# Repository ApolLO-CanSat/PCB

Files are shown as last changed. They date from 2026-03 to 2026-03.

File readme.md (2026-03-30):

# Team ApolLO's CanSat PCBs
The mainboard features:
- **RP2350A** MCU 
- **W25Q128JVPIQ** flash memory
- **Waveshare 23721** for GPS signal
- **RFM98W 433MHz** LoRa module
- **MPU-6050** gyroscope and accelerometer
- **BMP 280** barometer and thermometer
- **USB-C connector**
- **BOOTSEL** and **RESET** buttons
- Status **LED**
- **Buzzer** for easier recovery
\
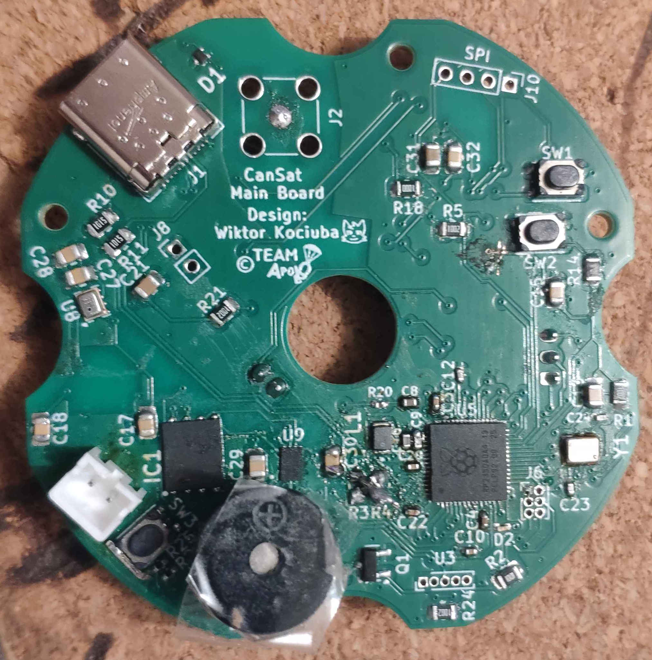
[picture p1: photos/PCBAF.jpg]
PCB Assembled Front

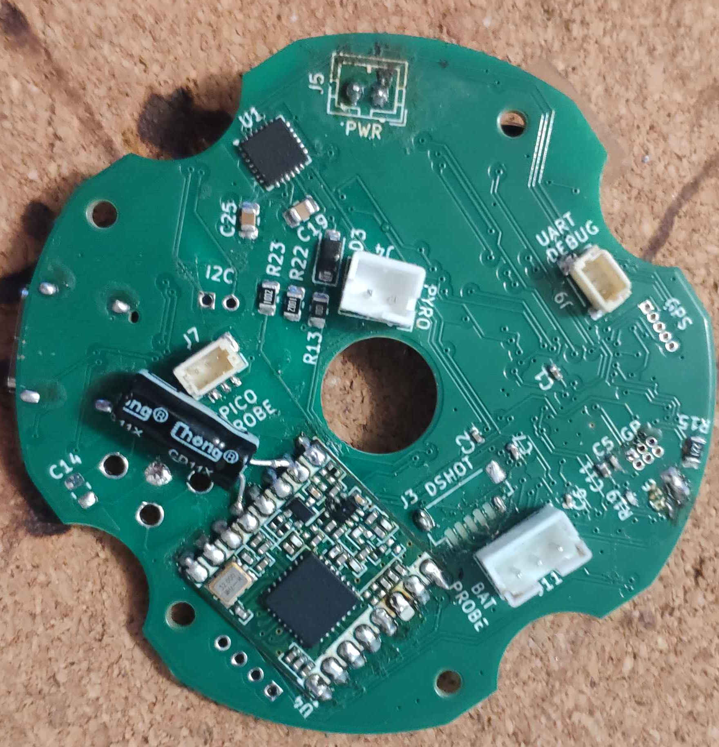
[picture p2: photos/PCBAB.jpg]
PCB Assembled Back

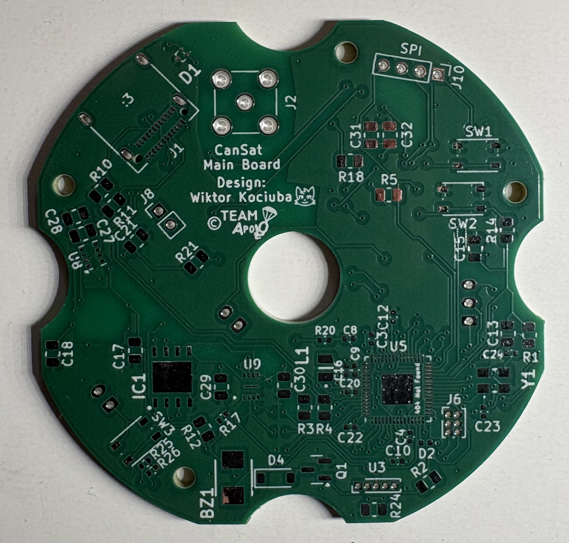
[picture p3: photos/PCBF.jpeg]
PCB Front

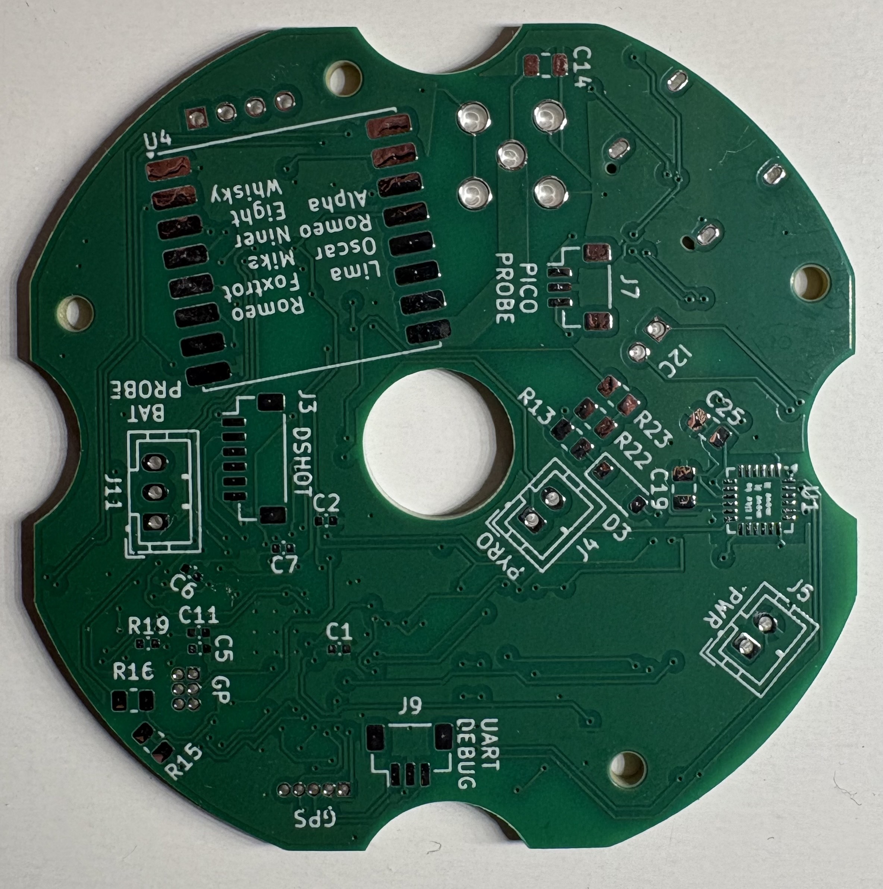
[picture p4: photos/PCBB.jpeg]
PCB Back

\
Mainboard schematic
MCU schematic
\
[Schematics in PDF file](https://github.com/ApolLO-CanSat/PCB/blob/main/schematics/CanSat.pdf)
\
PCB Schematic Front
PCB Schematic Back
\
[PCB schematic in PDF file](https://github.com/ApolLO-CanSat/PCB/blob/main/schematics/CanSatPCB.pdf)
---
## BOM
|Id|Designator|Footprint|Quantity|Designation|
|-|-|-|-|-|
|1|R5,R24,R12,R1,R21,R23,R22|R_0805_2012Metric|7|10K|
|2|R26,R25|R_0402_1005Metric|2|4.7K|
|3|C25|C_0805_2012Metric|1|10nF|
|4|R4,R3|R_0805_2012Metric|2|27|
|5|J8|PinHeader_1x02_P2.00mm_Vertical|1|Conn_01x02_Pin|
|6|L1|AOTAB201610S3R3101T|1|3.3u|
|7|D2|LED_0402_1005Metric|1|RED|
|8|U5|RP2350-QFN-60-1EP_7x7_P0.4mm_EP3.4x3.4mm_ThermalVias|1|RP2350_60QFN|
|9|C16,C9,C8,C11|C_0402_1005Metric|4|4.7uF|
|10|C20,C3,C4,C10,C22,C12,C7,C1,C5,C6,C2|C_0402_1005Metric|11|100nF|
|11|C24,C23|C_0402_1005Metric|2|15pF|
|12|C30,C15,C17,C32,C27,C28,C19|C_0805_2012Metric|7|100nF|
|13|BZ1|CMT-4023S|1|Buzzer|
|14|J1|USB_C_Receptacle_Amphenol_12401610E4-2A|1|USB_C_Receptacle|
|15|C31|C_0805_2012Metric|1|22u|
|16|SW2,SW1,SW3|SW_Push_1P1T_NO_Vertical_Wuerth_434133025816|3|SW_Push|
|17|IC1|SON127P600X500X80-9N-D|1|W25Q128JVPIQ|
|18|C21,C13|C_0805_2012Metric|2|1uF|
|19|D1|MMBT2907AM3T5G|1|ESD7L5.0DT5G|
|20|D4,D3|D_SOD-123|2|MBR0530T1G|
|21|R11,R10|R_0805_2012Metric|2|5.1K|
|22|J10|PinHeader_1x04_P2.00mm_Vertical|1|Conn_01x04_Pin|
|23|R18|R_0805_2012Metric|1|100|
|24|J2|SMA_Amphenol_901-144_Vertical|1|Conn_Coaxial|
|25|R17|R_0402_1005Metric|1|10K|
|26|R20|R_0402_1005Metric|1|33|
|27|U3|PinHeader_1x05_P1.00mm_Vertical|1|Waveshare23721|
|28|C18|C_0805_2012Metric|1|2.2nF|
|29|U8|Bosch_LGA-8_2x2.5mm_P0.65mm_ClockwisePinNumbering|1|BMP280|
|30|R2,R14,R13|R_0805_2012Metric|3|1K|
|31|Y1|ABM8272T3|1|ABM8272T3|
|32|C29|C_0805_2012Metric|1|2.2uF|
|33|Q1|SOT-23|1|BSS138|
|34|U9|PSON50P200X300X50-9N|1|APS6404L-3SQR-ZR|
|35|J6|PinHeader_2x03_P1.00mm_Vertical|1|Conn_01x06_Pin|
|36|R15|R_0805_2012Metric|1|220|
|37|J7|JST_SH_BM03B-SRSS-TB_1x03-1MP_P1.00mm_Vertical|1|Conn_01x03_Pin|
|38|R16|R_0805_2012Metric|1|DNC|
|39|J5|JST_PH_B2B-PH-K_1x02_P2.00mm_Vertical|1|Screw_Terminal_01x02|
|40|J9|JST_SH_BM03B-SRSS-TB_1x03-1MP_P1.00mm_Vertical|1|Conn_01x02_Pin|
|41|J11|JST_PH_B3B-PH-K_1x03_P2.00mm_Vertical|1|Conn_01x03_Socket|
|42|J3|JST_SH_BM06B-SRSS-TB_1x06-1MP_P1.00mm_Vertical|1|Conn_01x06_Socket|
|43|U4|HOPERF_RFM9XW_SMD|1|RFM98W-433S2|
|44|C14|C_0805_2012Metric|1|DNP|
|45|U1|InvenSense_QFN-24_4x4mm_P0.5mm|1|MPU-6050|
|46|J4|JST_PH_B2B-PH-K_1x02_P2.00mm_Vertical|1|Conn_01x02_Pin|
|47|R19|R_0402_1005Metric|1|1K|

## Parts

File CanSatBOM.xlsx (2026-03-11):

Id | Designator | Footprint | Quantity | Value | Manufacturer | Mfg Part # | Package | Type
1 | R4,R7,R3,R8,R9,R6,R5 | R_0805_2012Metric | 7 | 27 OHM | any available | any available | 0805(2012M) | SMD
2 | J8,J9,J4 | PinHeader_1x02_P1.00mm_Vertical | 3 | n/a | any available | any available | PinHeader_1x02_P1.00mm_Vertical | THT
3 | D2 | LED_0402_1005Metric | 1 | RED | any available | any available | 0402(1005M) | SMD
4 | U5 | RP2350-QFN-60-1EP_7x7_P0.4mm_EP3.4x3.4mm_ThermalVias | 1 | n/a | Raspberry Pi | RP2350A | SMD | SMD
5 | C30,C27,C28,C3,C4,C7,C10,C1,C5,C6,C12,C2 | CP_EIA-2012-15_AVX-P | 12 | 100nF | any available | any available | 2012-15M | SMD
6 | R23,R22,R12,R1,R2,R21 | R_0805_2012Metric | 6 | 10K OHM | any available | any available | 0805(2012M) | SMD
7 | BZ1 | MagneticBuzzer_Kingstate_KCG0601 | 1 | n/a | Kingstate | KCG0601 | THT | THT
8 | J1 | USB_C_Receptacle_Amphenol_12401610E4-2A | 1 | n/a | Amphenol | 12401610E4#2A | SMD | SMD
9 | C31 | CP_EIA-2012-15_AVX-P | 1 | 22uF | any available | any available | 2012-15M | SMD
10 | L1 | L_6.3x6.3_H3 | 1 | 3.3uH | any available | any available | L_6.3x6.3_H3 | SMD
11 | SW2,SW1,SW3 | SW_Push_1P1T_NO_Vertical_Wuerth_434133025816 | 3 | n/a | Wuerth | 434133025816 | SMD | SMD
12 | C15,C32 | CP_EIA-2012-15_AVX-P | 2 | 100nF | any available | any available | 2012-15M | SMD
13 | IC1 | SON127P600X500X80-9N-D | 1 | n/a | Winbond | W25Q128JVPIQ | SMD | SMD
14 | C21,C13,C14 | CP_EIA-2012-15_AVX-P | 3 | 1uF | any available | any available | 2012-15M | SMD
15 | C17 | CP_EIA-2012-15_AVX-P | 1 | 0.1uF | any available | any available | 2012-15M | SMD
16 | D1 | MMBT2907AM3T5G | 1 | n/a | onsemi | ESD7L5.0DT5G | SMD | SMD
17 | J7 | PinHeader_1x03_P1.00mm_Vertical | 1 | Conn_01x03_Pin | any available | any available | PinHeader_1x03_P1.00mm_Vertical | THT
18 | R11,R10 | R_0805_2012Metric | 2 | 5.1K Ohm | any available | any available | 0805(2012M) | SMD
19 | J10 | PinHeader_1x04_P1.00mm_Vertical | 1 | Conn_01x04_Pin | any available | any available | PinHeader_1x04_P1.00mm_Vertical | THT
20 | R18 | R_0805_2012Metric | 1 | 100 Ohm | any available | any available | 0805(2012M) | SMD
21 | C9,C16,C8,C11 | CP_EIA-2012-15_AVX-P | 4 | 4.7uF | any available | any available | 2012-15M | SMD
22 | J2 | SMA_Amphenol_901-144_Vertical | 1 | DNC | DNC | DNC | DNC | DNC
23 | R20 | R_0805_2012Metric | 1 | 33 Ohm | any available | any available | 0805(2012M) | SMD
24 | U3 | PinHeader_1x05_P1.00mm_Vertical | 1 | Conn_01x05_Pin | any available | any available | PinHeader_1x05_P1.00mm_Vertical | THT
25 | C18,C19 | CP_EIA-2012-15_AVX-P | 2 | 2.2nF | any available | any available | 2012-15M | SMD
26 | Y2 | ASE12000MHzET | 1 | n/a | Abracon | ASE-12.000MHz-E-T | SMD | SMD
27 | U8 | Bosch_LGA-8_2x2.5mm_P0.65mm_ClockwisePinNumbering | 1 | n/a | Bosch | BMP280 | SMD | SMD
28 | C29 | CP_EIA-2012-15_AVX-P | 1 | 2.2uF | any available | any available | 2012-15M | SMD
29 | U9 | PSON50P200X300X50-9N | 1 | n/a | AP Memory | APS6404L-3SQR-ZR | SMD | SMD
30 | J6 | PinHeader_2x03_P1.00mm_Vertical | 1 | Conn_01x06_Pin | any available | any available | PinHeader_2x03_P1.00mm_Vertical | THT
31 | R14,R13 | R_0805_2012Metric | 2 | 1K Ohm | any available | any available | 0805(2012M) | SMD
32 | R15 | R_0805_2012Metric | 1 | 220 Ohm | any available | any available | 0805(2012M) | SMD
33 | R16 | R_0805_2012Metric | 1 | DNC | DNC | DNC | DNC | DNC
34 | J5 | TerminalBlock_bornier-2_P5.08mm | 1 | Screw_Terminal_01x02 | any available | any available | Screw_Terminal_01x02 | THT
35 | J3 | JST_SH_BM06B-SRSS-TB_1x06-1MP_P1.00mm_Vertical | 1 | Conn_01x06_Socket | JST | BM06B-SRSS-TB (LF)(SN) | SMD | SMD
36 | U4 | HOPERF_RFM9XW_SMD | 1 | n/a | RF Solutions | RFM98W-433S2 | SMD | SMD
37 | D3 | D_SOD-123 | 1 | n/a | onsemi | MBR0530 | SMD | SMD
38 | U1 | InvenSense_QFN-24_4x4mm_P0.5mm | 1 | n/a | InvenSense | MPU-6050 | SMD | SMD

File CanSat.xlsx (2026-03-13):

Id | Designator | Footprint | Quantity | Designation | Part #
1 | R4,R7,R3,R8,R9,R6,R5 | R_0805_2012Metric | 7 | 27 | AC0805FR-0727RL | 0.039 | 0.273
2 | J8,J9,J4 | PinHeader_1x02_P1.00mm_Vertical | 3 | Conn_01x02_Pin |  |  | 0
3 | L1 | AOTAB201610S3R3101T | 1 | 3.3u | ISC1210ER3R3K | 2.4 | 2.4
4 | D2 | LED_0402_1005Metric | 1 | RED | IN-S42DS5G | 1.55 | 1.55
5 | U5 | RP2350-QFN-60-1EP_7x7_P0.4mm_EP3.4x3.4mm_ThermalVias | 1 | RP2350_60QFN | SC1509(13)-A4 | 2.97 | 2.97
6 | C16,C9,C8,C11 | C_0402_1005Metric | 4 | 4.7uF | 0402ZD475KAT2A | 0.593 | 2.372
7 | C20,C3,C4,C10,C22,C12,C7,C1,C5,C6,C2 | C_0402_1005Metric | 11 | 100nF | 0402ZC104KAT4A | 0.12 | 1.32
8 | C24,C23 | C_0402_1005Metric | 2 | 15pF | C0402C150F8HACTU | 0.628 | 1.256
9 | C30,C15,C17,C32,C27,C28 | CP_EIA-2012-15_AVX-P | 6 | 100nF | KAF21BR71H104JM | 0.335 | 2.01
10 | BZ1 | CMT-4023S | 1 | Buzzer | CMT-4023S-SMT-TR | 11.35 | 11.35
11 | J1 | USB_C_Receptacle_Amphenol_12401610E4-2A | 1 | USB_C_Receptacle | 12401610E4#2A | 5.33 | 5.33
12 | C31 | CP_EIA-2012-15_AVX-P | 1 | 22u | CL21A226MQQNNNE | 0.482 | 0.482
13 | SW2,SW1,SW3 | SW_Push_1P1T_NO_Vertical_Wuerth_434133025816 | 3 | SW_Push | 434133025816 | 2.03 | 6.09
14 | IC1 | SON127P600X500X80-9N-D | 1 | W25Q128JVPIQ | W25Q128JVPIQ | 8.51 | 8.51
15 | C21,C13 | CP_EIA-2012-15_AVX-P | 2 | 1uF | 0805YC105KAT2A | 0.37 | 0.74
16 | R12,R1,R21,R23,R22 | R_0805_2012Metric | 5 | 10K | AC0805DR-0710KL | 0.112 | 0.56
17 | D1 | MMBT2907AM3T5G | 1 | ESD7L5.0DT5G | ESD7L5.0DT5G | 4.21 | 4.21
18 | J7 | PinHeader_1x03_P1.00mm_Vertical | 1 | Conn_01x03_Pin |  |  | 0
19 | R11,R10 | R_0805_2012Metric | 2 | 5.1K | RC0805FR-075K1L | 0.37 | 0.74
20 | J10 | PinHeader_1x04_P1.00mm_Vertical | 1 | Conn_01x04_Pin |  |  | 0
21 | R18 | R_0805_2012Metric | 1 | 100 | RC0805FR-07100RL | 0.37 | 0.37
22 | J2 | SMA_Amphenol_901-144_Vertical | 1 | Conn_Coaxial |  |  | 0
23 | R17 | R_0402_1005Metric | 1 | 10K | RCA040210K0JNED | 0.142 | 0.142
24 | R20 | R_0402_1005Metric | 1 | 33 | SFR01MZPJ330 | 0.555 | 0.555
25 | U3 | PinHeader_1x05_P1.00mm_Vertical | 1 | Waveshare23721 |  |  | 0
26 | C18,C19 | CP_EIA-2012-15_AVX-P | 2 | 2.2nF | 08055C222M4T2A | 0.778 | 1.556
27 | U8 | Bosch_LGA-8_2x2.5mm_P0.65mm_ClockwisePinNumbering | 1 | BMP280 | BMP280 |  | 0
28 | Y1 | ABM8272T3 | 1 | ABM8272T3 | ABM8-272-T3 | 2 | 2
29 | C29 | CP_EIA-2012-15_AVX-P | 1 | 2.2uF | 0805X225M100CT | 0.512 | 0.512
30 | U9 | PSON50P200X300X50-9N | 1 | APS6404L-3SQR-ZR | APS6404L-3SQR-ZR | 8.08 | 8.08
31 | J6 | PinHeader_2x03_P1.00mm_Vertical | 1 | Conn_01x06_Pin |  |  | 0
32 | R14,R13 | R_0805_2012Metric | 2 | 1K | 1623131-1 | 0.37 | 0.74
33 | R15 | R_0805_2012Metric | 1 | 220 | RC0805JR-13220RL | 0.026 | 0.026
34 | R16 | R_0805_2012Metric | 1 | DNC |  |  | 0
35 | J5 | TerminalBlock_bornier-2_P5.08mm | 1 | Screw_Terminal_01x02 |  |  | 0
36 | J3 | JST_SH_BM06B-SRSS-TB_1x06-1MP_P1.00mm_Vertical | 1 | Conn_01x06_Socket | BM06B-SRSS-TB(LF)(SN) | 3.33 | 3.33
37 | U4 | HOPERF_RFM9XW_SMD | 1 | RFM98W-433S2 | RFM98W-433S2 |  | 0
38 | D3 | D_SOD-123 | 1 | MBR0530 | MBR0530T1G | 0.516 | 0.516
39 | U1 | InvenSense_QFN-24_4x4mm_P0.5mm | 1 | MPU-6050 | MPU-6050 |  | 0
40 | R19 | R_0402_1005Metric | 1 | 1K | MCS04020C1001FE000 | 0.086 | 0.086
 |  |  |  |  |  |  | 70.076
 |  |  |  |  |  | Quantity | 2
 |  |  |  |  |  |  | 140.152

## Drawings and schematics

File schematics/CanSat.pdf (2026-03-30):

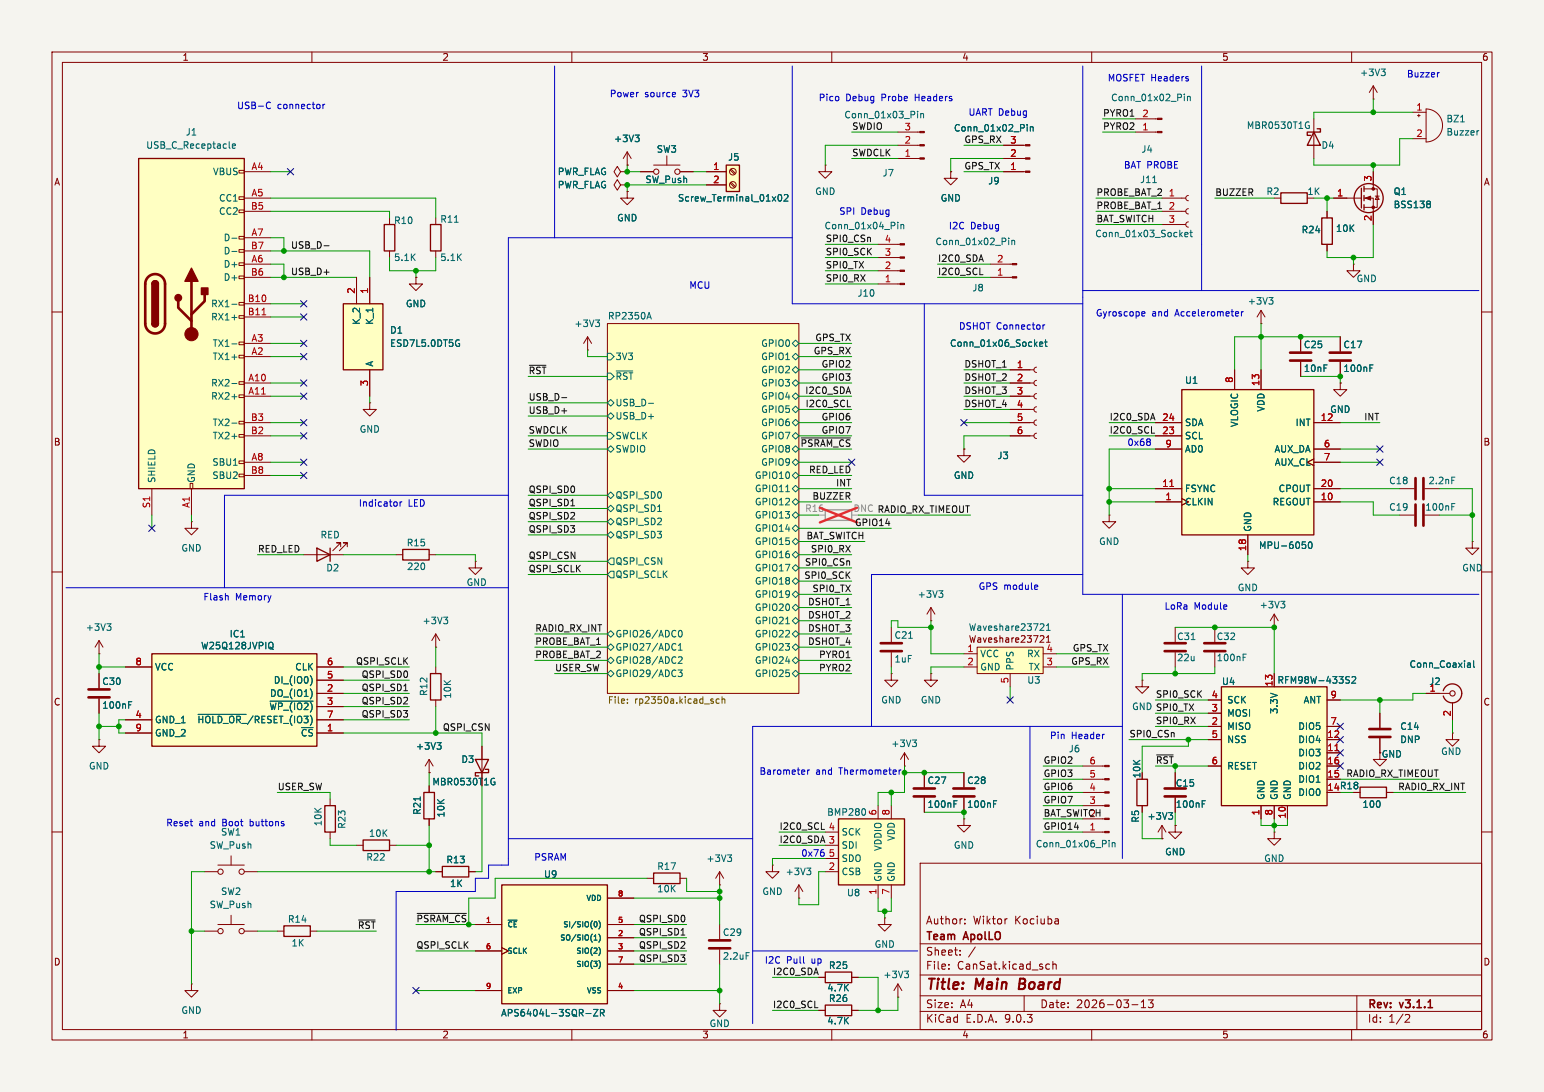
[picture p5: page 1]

Reset and Boot buttons

File: CanSat.kicad_sch Sheet: / Team ApolLO

Id: 1/2 Title: Main Board

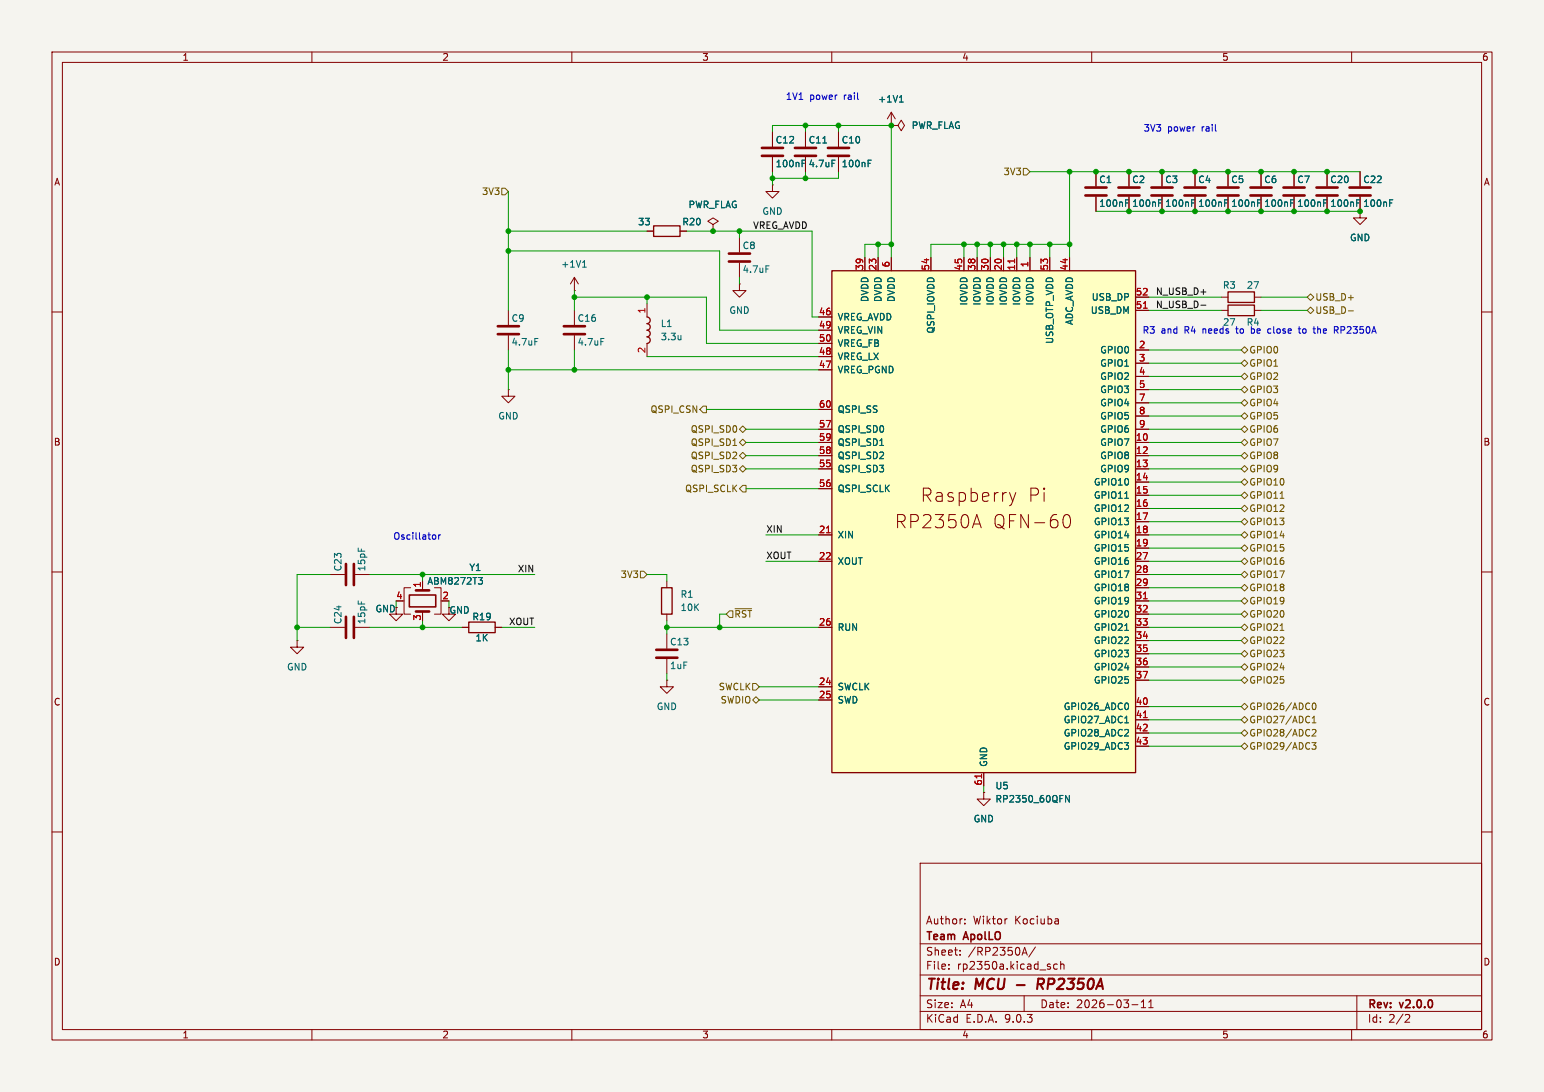
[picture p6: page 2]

6 QSPI_IOVDD 54 IOVDD 45 IOVDD 38 GND 61 IOVDD 30 IOVDD 20 IOVDD 11 IOVDD

File: rp2350a.kicad_sch Sheet: /RP2350A/ Team ApolLO

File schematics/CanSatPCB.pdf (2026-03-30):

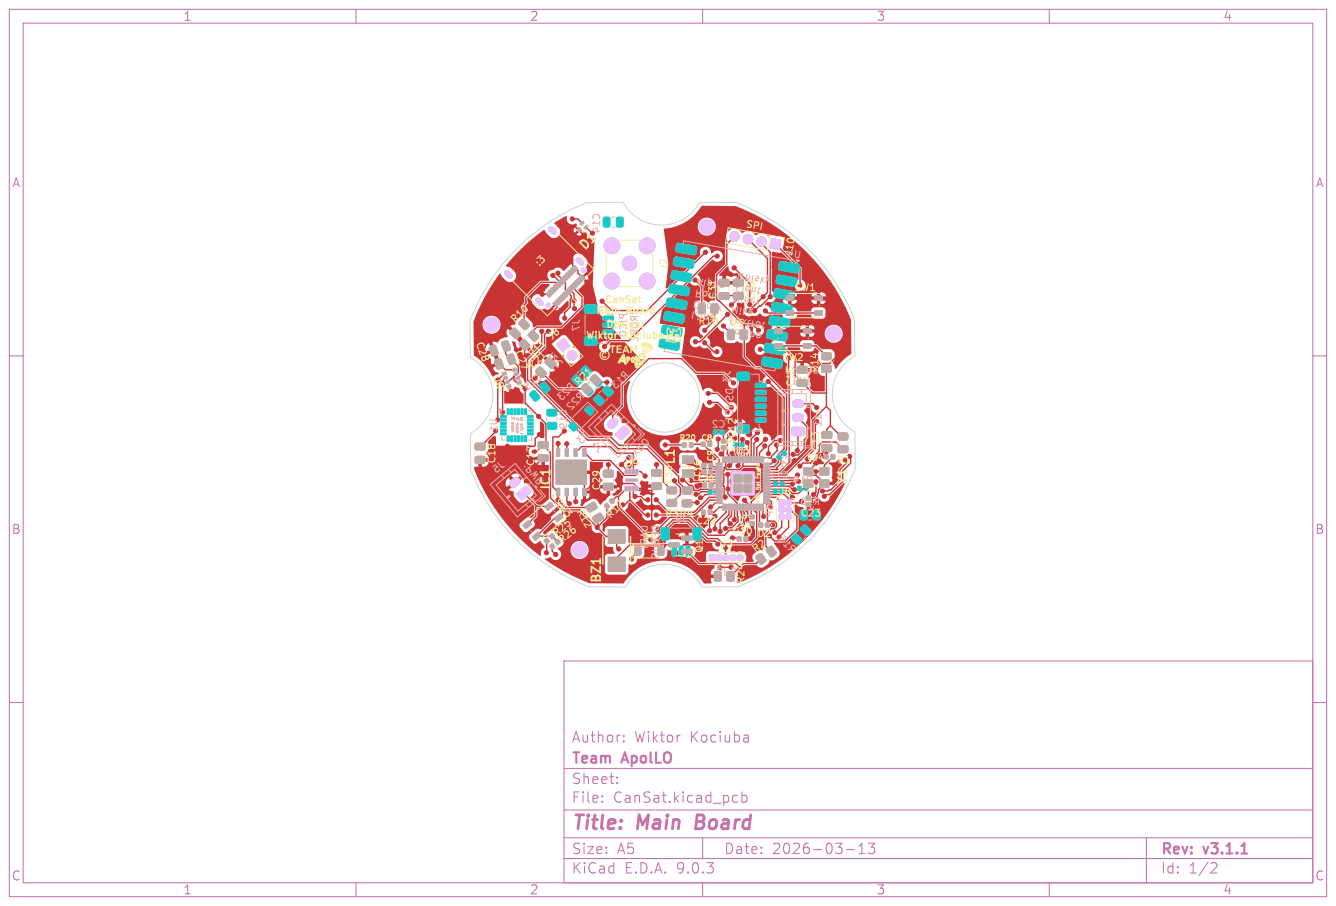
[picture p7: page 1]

File: CanSat.kicad_pcb Sheet: Team ApolLO

Id: 1/2 Title: Main Board

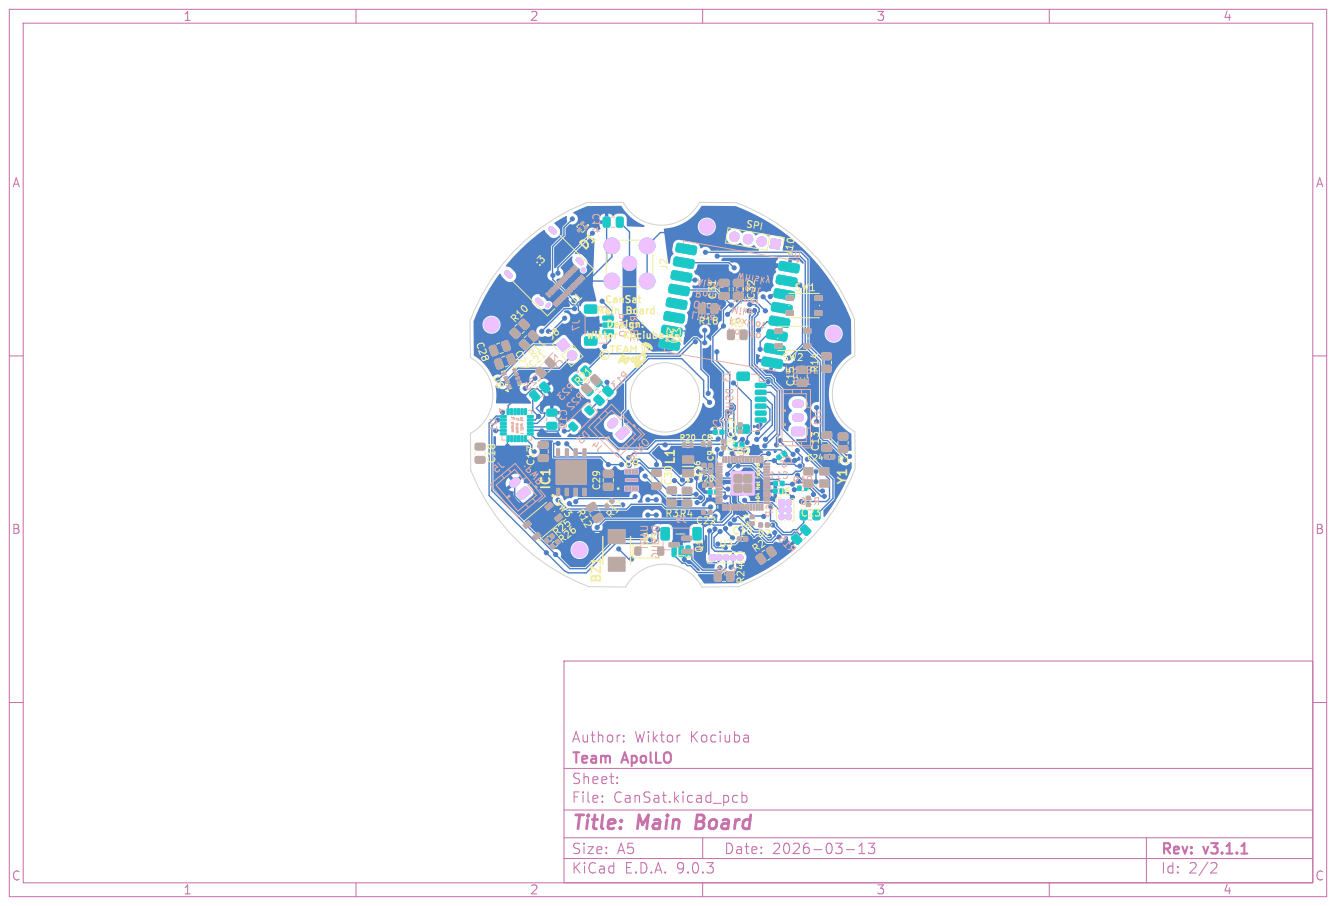
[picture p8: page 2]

File: CanSat.kicad_pcb Sheet: Team ApolLO

Id: 2/2 Title: Main Board

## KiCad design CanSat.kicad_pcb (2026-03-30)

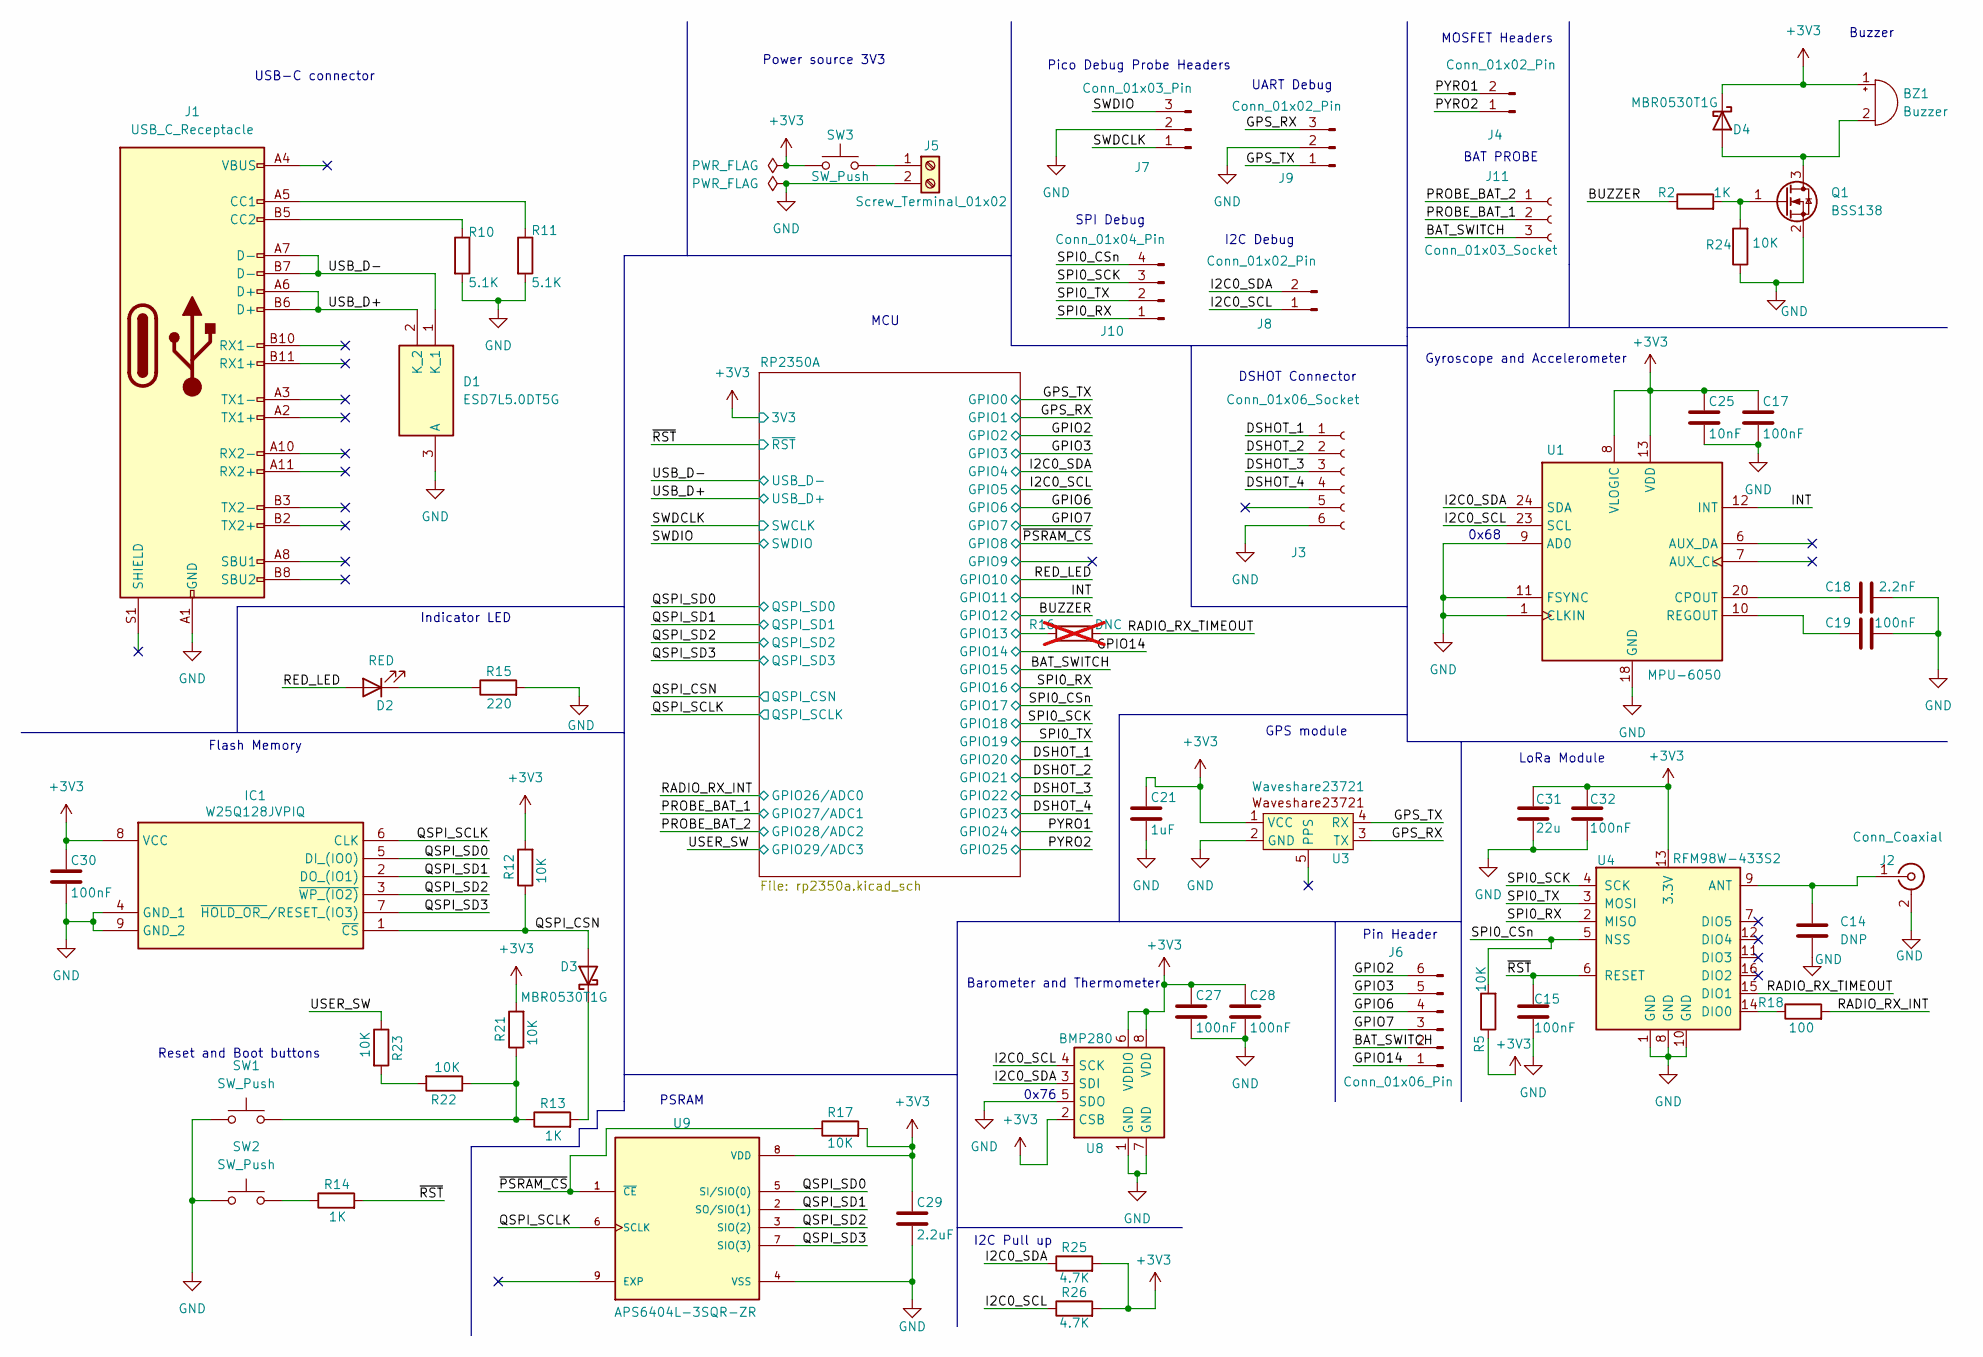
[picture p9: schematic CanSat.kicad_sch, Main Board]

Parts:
BZ1: Buzzer; CMT-4023S
C14: DNP; C_0805_2012Metric
C15, C17, C19, C27, C28, C30, C32: 100nF; C_0805_2012Metric
C18: 2.2nF; C_0805_2012Metric
C21: 1uF; C_0805_2012Metric
C25: 10nF; C_0805_2012Metric
C29: 2.2uF; C_0805_2012Metric
C31: 22u; C_0805_2012Metric
D1: ESD7L5.0DT5G; MMBT2907AM3T5G; Mouser Part Number 863-ESD7L5.0DT5G
D2: RED; LED_0402_1005Metric
D3, D4: MBR0530T1G; D_SOD-123
IC1: W25Q128JVPIQ; SON127P600X500X80-9N-D; Mouser Part Number 454-W25Q128JVPIQ
J1: USB_C_Receptacle; USB_C_Receptacle_Amphenol_12401610E4-2A
J2: Conn_Coaxial; SMA_Amphenol_901-144_Vertical
J3: Conn_01x06_Socket; JST_SH_BM06B-SRSS-TB_1x06-1MP_P1.00mm_Vertical
J4: Conn_01x02_Pin; JST_PH_B2B-PH-K_1x02_P2.00mm_Vertical
J5: Screw_Terminal_01x02; JST_PH_B2B-PH-K_1x02_P2.00mm_Vertical
J6: Conn_01x06_Pin; PinHeader_2x03_P1.00mm_Vertical
J7: Conn_01x03_Pin; JST_SH_BM03B-SRSS-TB_1x03-1MP_P1.00mm_Vertical
J8: Conn_01x02_Pin; PinHeader_1x02_P2.00mm_Vertical
J9: Conn_01x02_Pin; JST_SH_BM03B-SRSS-TB_1x03-1MP_P1.00mm_Vertical
J10: Conn_01x04_Pin; PinHeader_1x04_P2.00mm_Vertical
J11: Conn_01x03_Socket; JST_PH_B3B-PH-K_1x03_P2.00mm_Vertical
Q1: BSS138; SOT-23
R2, R13, R14: 1K; R_0805_2012Metric
R5, R12, R21, R22, R23, R24: 10K; R_0805_2012Metric
R10, R11: 5.1K; R_0805_2012Metric
R15: 220; R_0805_2012Metric
R16: DNC; R_0805_2012Metric; not fitted
R17: 10K; R_0402_1005Metric
R18: 100; R_0805_2012Metric
R25, R26: 4.7K; R_0402_1005Metric
SW1, SW2, SW3: SW_Push; SW_Push_1P1T_NO_Vertical_Wuerth_434133025816
U1: MPU-6050; InvenSense_QFN-24_4x4mm_P0.5mm
U3: Waveshare23721; PinHeader_1x05_P1.00mm_Vertical
U4: RFM98W-433S2; HOPERF_RFM9XW_SMD
U8: BMP280; Bosch_LGA-8_2x2.5mm_P0.65mm_ClockwisePinNumbering
U9: APS6404L-3SQR-ZR; PSON50P200X300X50-9N; PARTREV 2.3

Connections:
+3V3: BZ1.1 (+), C17.1, C21.1, C25.1, C27.1, C28.1, C29.1, C30.1, C31.1, C32.1, D4.1 (K), IC1.8 (VCC), R5.1, R12.2, R17.2, R21.2, R25.2, R26.2, SW3.1, U1.8 (VLOGIC), U1.13 (VDD), U3.1 (VCC), U4.13 (3.3V), U8.2 (CSB), U8.6 (VDDIO), U8.8 (VDD), U9.8 (VDD); also elsewhere on the board
/BAT_SWITCH: J6.2, J11.3; also elsewhere on the board
/BUZZER: R2.1; also elsewhere on the board
/DSHOT_1: J3.1; also elsewhere on the board
/DSHOT_2: J3.2; also elsewhere on the board
/DSHOT_3: J3.3; also elsewhere on the board
/DSHOT_4: J3.4; also elsewhere on the board
/GPIO2: J6.6; also elsewhere on the board
/GPIO3: J6.5; also elsewhere on the board
/GPIO6: J6.4; also elsewhere on the board
/GPIO7: J6.3; also elsewhere on the board
/GPIO14: J6.1; also elsewhere on the board
/GPS_RX: J9.3, U3.3 (TX); also elsewhere on the board
/GPS_TX: J9.1, U3.4 (RX); also elsewhere on the board
/I2C0_SCL: J8.1, R26.1, U1.23 (SCL), U8.4 (SCK); also elsewhere on the board
/I2C0_SDA: J8.2, R25.1, U1.24 (SDA), U8.3 (SDI); also elsewhere on the board
/INT: U1.12 (INT); also elsewhere on the board
/PROBE_BAT_1: J11.2; also elsewhere on the board
/PROBE_BAT_2: J11.1; also elsewhere on the board
/PYRO1: J4.2; also elsewhere on the board
/PYRO2: J4.1; also elsewhere on the board
/QSPI_CSN: D3.2 (A), IC1.1 (~CS), R12.1; also elsewhere on the board
/QSPI_SCLK: IC1.6 (CLK), U9.6 (SCLK); also elsewhere on the board
/QSPI_SD0: IC1.5 (DI_(IO0)), U9.5 (SI/SIO(0)); also elsewhere on the board
/QSPI_SD1: IC1.2 (DO_(IO1)), U9.2 (SO/SIO(1)); also elsewhere on the board
/QSPI_SD2: IC1.3 (~WP_(IO2)), U9.3 (SIO(2)); also elsewhere on the board
/QSPI_SD3: IC1.7 (~HOLD_OR_/RESET_(IO3)), U9.7 (SIO(3)); also elsewhere on the board
/RADIO_RX_INT: R18.2; also elsewhere on the board
/RADIO_RX_TIMEOUT: R16.2, U4.15 (DIO1)
/RED_LED: D2.2 (A); also elsewhere on the board
/RP2350A/GPIO13: R16.1; also elsewhere on the board
/SPI0_CSn: J10.4, R5.2, U4.5 (NSS); also elsewhere on the board
/SPI0_RX: J10.1, U4.2 (MISO); also elsewhere on the board
/SPI0_SCK: J10.3, U4.4 (SCK); also elsewhere on the board
/SPI0_TX: J10.2, U4.3 (MOSI); also elsewhere on the board
/SWDCLK: J7.1; also elsewhere on the board
/SWDIO: J7.3; also elsewhere on the board
/USB_D+: D1.2 (K_2), J1.A6 (D+), J1.B6 (D+); also elsewhere on the board
/USB_D-: D1.1 (K_1), J1.A7 (D-), J1.B7 (D-); also elsewhere on the board
/USER_SW: R23.1; also elsewhere on the board
/~PSRAM_CS: R17.1, U9.1 (~CE); also elsewhere on the board
/~RST: C15.1, R14.2, U4.6 (RESET); also elsewhere on the board
GND: C14.1, C15.2, C17.2, C18.2, C19.2, C21.2, C25.2, C27.2, C28.2, C29.2, C30.2, C31.2, C32.2, D1.3 (A), IC1.4 (GND_1), IC1.9 (GND_2), J1.A1 (GND), J1.A12 (GND), J1.B1 (GND), J1.B12 (GND), J2.2 (Ext), J3.6, J5.2, J7.2, J9.2, Q1.2 (S), R10.2, R11.2, R15.2, R24.1, SW1.1, SW2.1, U1.1 (CLKIN), U1.9 (AD0), U1.11 (FSYNC), U1.18 (GND), U3.2 (GND), U4.1 (GND), U4.8 (GND), U4.10 (GND), U8.1 (GND), U8.5 (SDO), U8.7 (GND), U9.4 (VSS); also elsewhere on the board
unnamed: BZ1.2 (-), D4.2 (A), Q1.3 (D)
unnamed: D2.1 (K), R15.1
unnamed: D3.1 (K), R13.2
unnamed: J1.A5 (CC1), R11.1
unnamed: J1.B5 (CC2), R10.1
unnamed: C14.2, J2.1 (In), U4.9 (ANT)
unnamed: J5.1, SW3.2
unnamed: Q1.1 (G), R2.2, R24.2
unnamed: R13.1, R21.1, R22.1, SW1.2
unnamed: R14.1, SW2.2
unnamed: R22.2, R23.2
unnamed: C18.1, U1.20 (CPOUT)
unnamed: C19.1, U1.10 (REGOUT)
unnamed: R18.1, U4.14 (DIO0)

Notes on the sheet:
I2C Pull up
0x68
BAT PROBE
UART Debug
Buzzer
Gyroscope and Accelerometer
Reset and Boot buttons
GPS module
LoRa Module
MOSFET Headers
Power source 3V3
Pin Header
I2C Debug
PSRAM
Pico Debug Probe Headers
MCU
0x76
SPI Debug
Barometer and Thermometer
USB-C connector
Indicator LED
Flash Memory
DSHOT Connector

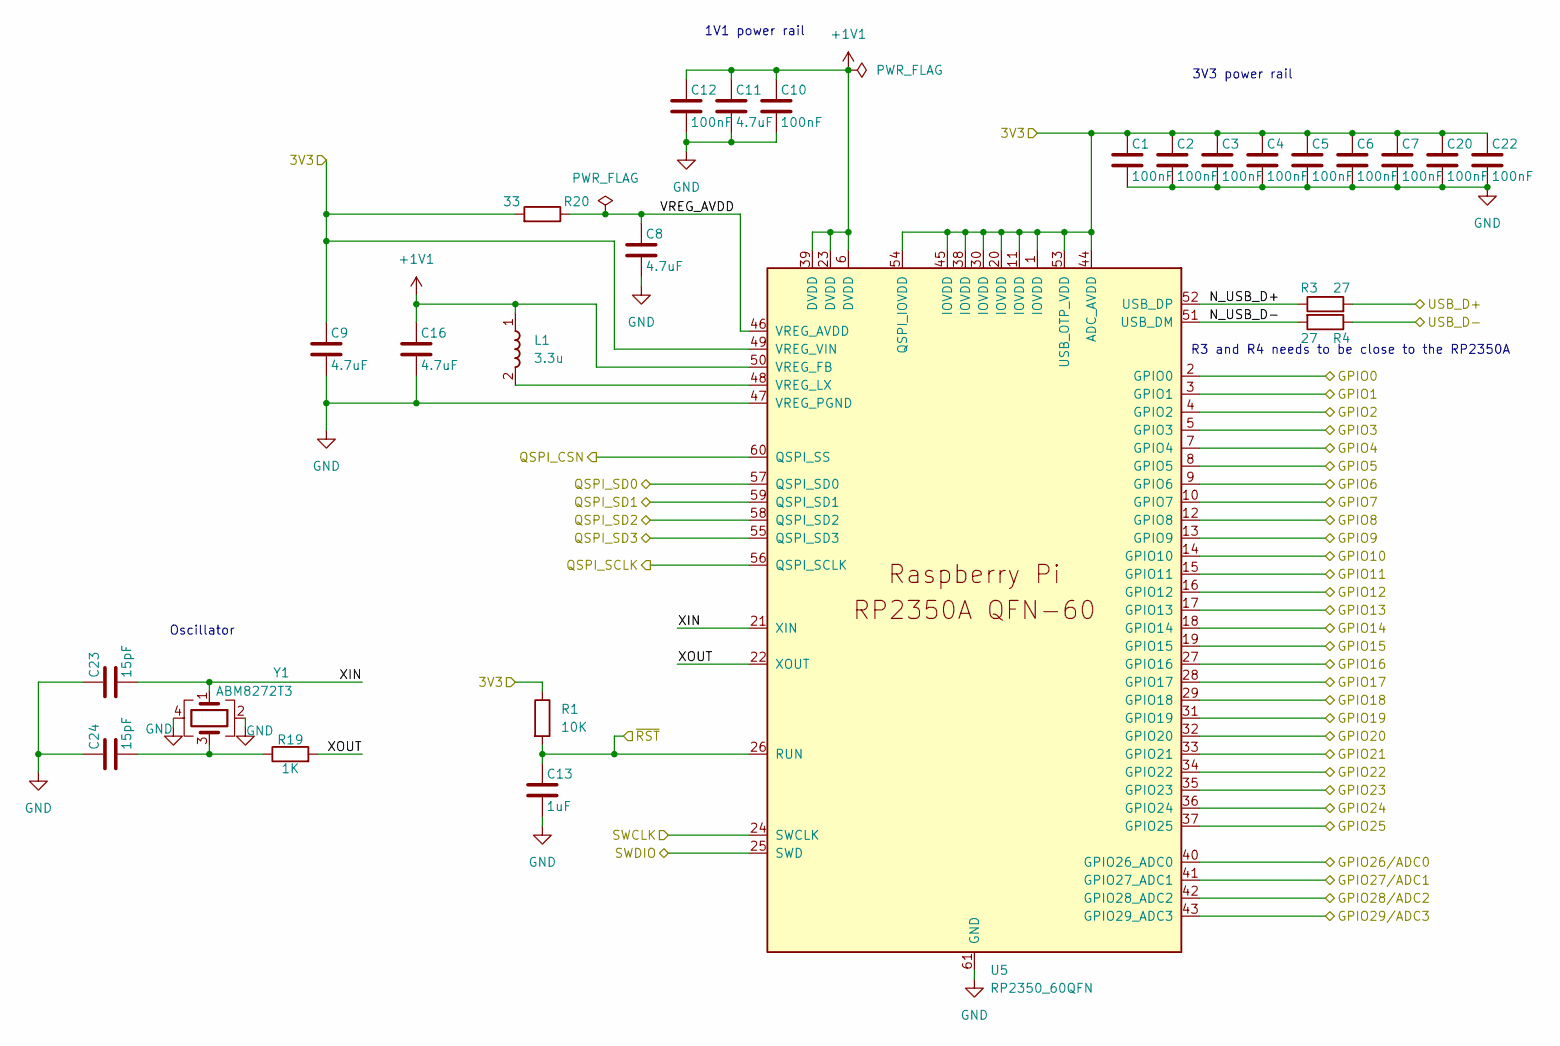
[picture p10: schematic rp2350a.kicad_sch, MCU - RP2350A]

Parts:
C1, C2, C3, C4, C5, C6, C7, C10, C12, C20, C22: 100nF; C_0402_1005Metric
C8, C9, C11, C16: 4.7uF; C_0402_1005Metric
C13: 1uF; C_0805_2012Metric
C23, C24: 15pF; C_0402_1005Metric
L1: 3.3u; AOTAB201610S3R3101T; Mouser Part Number 815-AB201610S3R3101T
R1: 10K; R_0805_2012Metric
R3, R4: 27; R_0805_2012Metric
R19: 1K; R_0402_1005Metric
R20: 33; R_0402_1005Metric
U5: RP2350_60QFN; RP2350-QFN-60-1EP_7x7_P0.4mm_EP3.4x3.4mm_ThermalVias
Y1: ABM8272T3

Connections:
+1V1: C10.1, C11.1, C12.1, C16.1, L1.1, U5.6 (DVDD), U5.23 (DVDD), U5.39 (DVDD), U5.50 (VREG_FB)
+3V3: C1.1, C2.1, C3.1, C4.1, C5.1, C6.1, C7.1, C9.1, C20.1, C22.1, R1.1, R20.2, U5.1 (IOVDD), U5.11 (IOVDD), U5.20 (IOVDD), U5.30 (IOVDD), U5.38 (IOVDD), U5.44 (ADC_AVDD), U5.45 (IOVDD), U5.49 (VREG_VIN), U5.53 (USB_OTP_VDD), U5.54 (QSPI_IOVDD); also elsewhere on the board
/BAT_SWITCH: U5.19 (GPIO15); also elsewhere on the board
/BUZZER: U5.16 (GPIO12); also elsewhere on the board
/DSHOT_1: U5.32 (GPIO20); also elsewhere on the board
/DSHOT_2: U5.33 (GPIO21); also elsewhere on the board
/DSHOT_3: U5.34 (GPIO22); also elsewhere on the board
/DSHOT_4: U5.35 (GPIO23); also elsewhere on the board
/GPIO2: U5.4 (GPIO2); also elsewhere on the board
/GPIO3: U5.5 (GPIO3); also elsewhere on the board
/GPIO6: U5.9 (GPIO6); also elsewhere on the board
/GPIO7: U5.10 (GPIO7); also elsewhere on the board
/GPIO14: U5.18 (GPIO14); also elsewhere on the board
/GPS_RX: U5.3 (GPIO1); also elsewhere on the board
/GPS_TX: U5.2 (GPIO0); also elsewhere on the board
/I2C0_SCL: U5.8 (GPIO5); also elsewhere on the board
/I2C0_SDA: U5.7 (GPIO4); also elsewhere on the board
/INT: U5.15 (GPIO11); also elsewhere on the board
/PROBE_BAT_1: U5.41 (GPIO27_ADC1); also elsewhere on the board
/PROBE_BAT_2: U5.42 (GPIO28_ADC2); also elsewhere on the board
/PYRO1: U5.36 (GPIO24); also elsewhere on the board
/PYRO2: U5.37 (GPIO25); also elsewhere on the board
/QSPI_CSN: U5.60 (QSPI_SS); also elsewhere on the board
/QSPI_SCLK: U5.56 (QSPI_SCLK); also elsewhere on the board
/QSPI_SD0: U5.57 (QSPI_SD0); also elsewhere on the board
/QSPI_SD1: U5.59 (QSPI_SD1); also elsewhere on the board
/QSPI_SD2: U5.58 (QSPI_SD2); also elsewhere on the board
/QSPI_SD3: U5.55 (QSPI_SD3); also elsewhere on the board
/RADIO_RX_INT: U5.40 (GPIO26_ADC0); also elsewhere on the board
/RED_LED: U5.14 (GPIO10); also elsewhere on the board
/RP2350A/GPIO9: U5.13 (GPIO9)
/RP2350A/GPIO13: U5.17 (GPIO13); also elsewhere on the board
/RP2350A/N_USB_D+: R3.1, U5.52 (USB_DP)
/RP2350A/N_USB_D-: R4.2, U5.51 (USB_DM)
/RP2350A/VREG_AVDD: C8.1, R20.1, U5.46 (VREG_AVDD)
/RP2350A/XIN: C23.2, U5.21 (XIN), Y1.1
/RP2350A/XOUT: R19.2, U5.22 (XOUT)
/SPI0_CSn: U5.28 (GPIO17); also elsewhere on the board
/SPI0_RX: U5.27 (GPIO16); also elsewhere on the board
/SPI0_SCK: U5.29 (GPIO18); also elsewhere on the board
/SPI0_TX: U5.31 (GPIO19); also elsewhere on the board
/SWDCLK: U5.24 (SWCLK); also elsewhere on the board
/SWDIO: U5.25 (SWD); also elsewhere on the board
/USB_D+: R3.2; also elsewhere on the board
/USB_D-: R4.1; also elsewhere on the board
/USER_SW: U5.43 (GPIO29_ADC3); also elsewhere on the board
/~PSRAM_CS: U5.12 (GPIO8); also elsewhere on the board
/~RST: C13.1, R1.2, U5.26 (RUN); also elsewhere on the board
GND: C1.2, C2.2, C3.2, C4.2, C5.2, C6.2, C7.2, C8.2, C9.2, C10.2, C11.2, C12.2, C13.2, C16.2, C20.2, C22.2, C23.1, C24.1, U5.47 (VREG_PGND), U5.61 (GND), Y1.2, Y1.4; also elsewhere on the board
unnamed: C24.2, R19.1, Y1.3
unnamed: L1.2, U5.48 (VREG_LX)

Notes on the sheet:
1V1 power rail
R3 and R4 needs to be close to the RP2350A
3V3 power rail
Oscillator

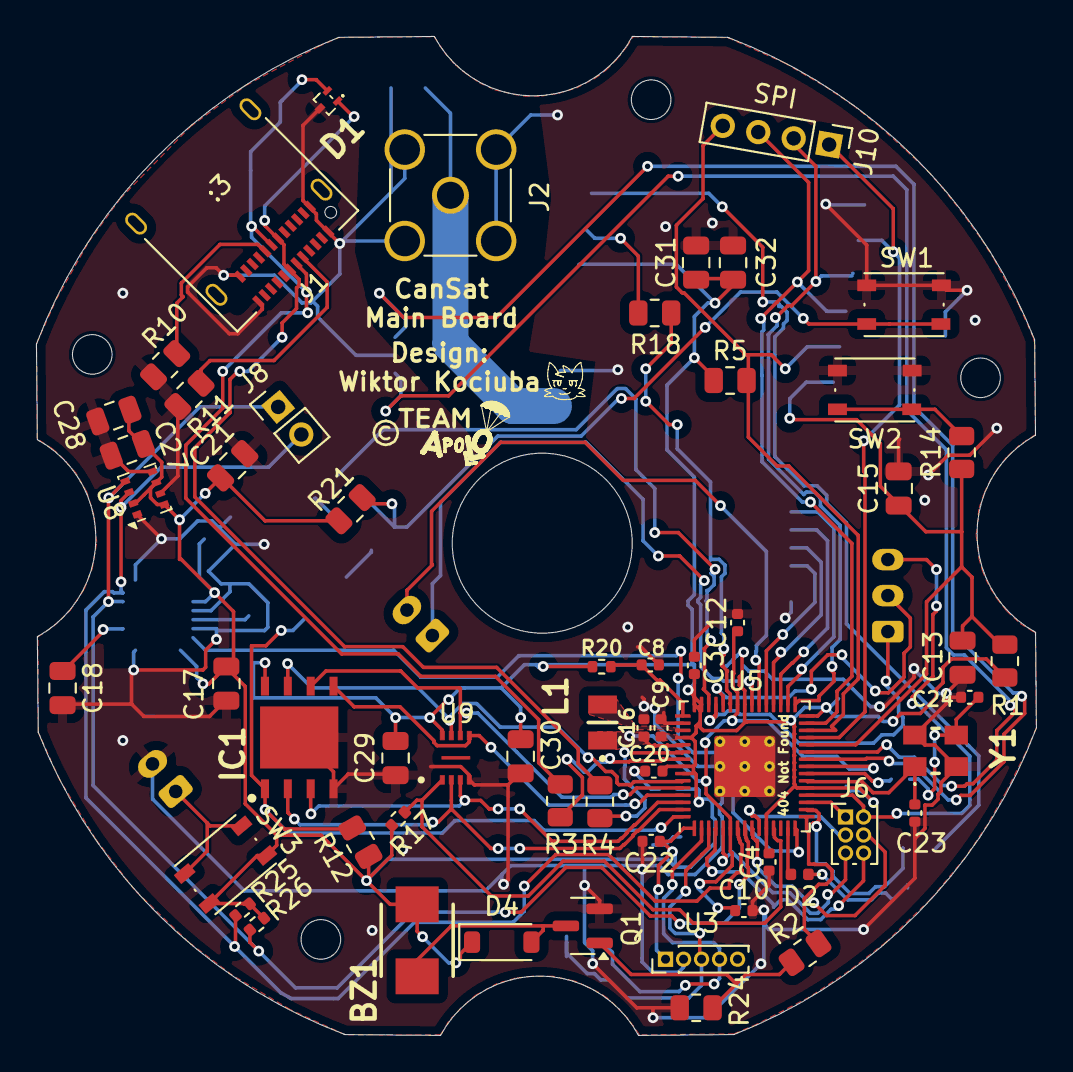
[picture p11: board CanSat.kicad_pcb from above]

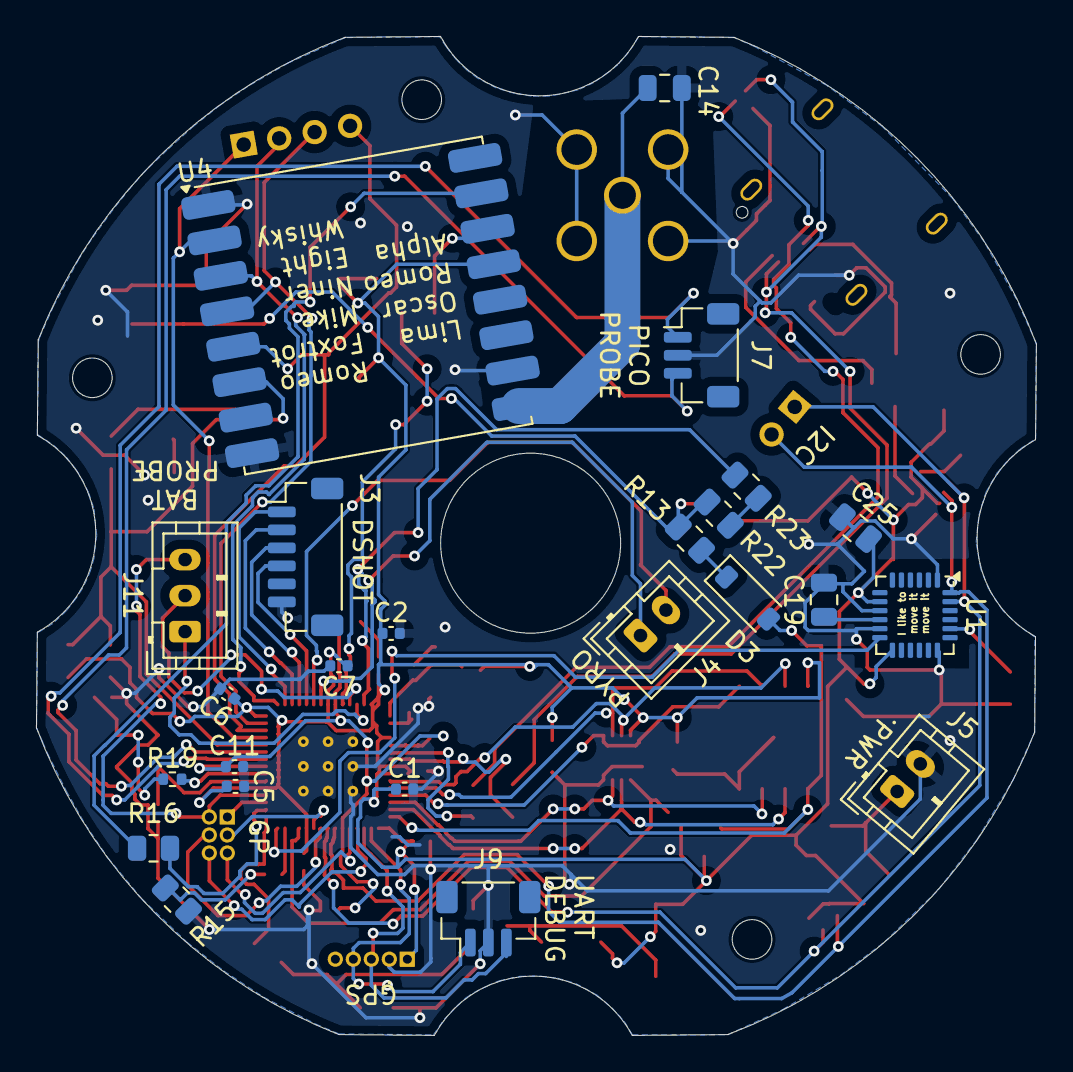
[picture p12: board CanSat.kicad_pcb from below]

Board: 2 copper layers, 55.6 x 55.5 mm, 84 parts (24 on the bottom side), 65 nets.

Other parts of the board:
M2, M2#2: MountingHole_2.2mm_M2

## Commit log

2025-11-21 Add new flash memory and PSRAM
    [CanSat.kicad_sch, radio.kicad_sch]
2025-11-21 Add new LoRa module
    [CanSat.kicad_sch, radio.kicad_sch]
2025-11-21 Assigned footprints and drew pcb outline
    [CanSat.kicad_pcb, CanSat.kicad_sch, radio.kicad_sch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]
2025-11-22 Add components to pcb
    Added:
    3V3 power source
    USB-C connector
    Flash memory and PSRAM
    [CanSat.kicad_pcb, CanSat.kicad_sch]
2025-12-10 Connected LoRa
    [CanSat.kicad_pcb, CanSat.kicad_sch]
2025-12-10 Added more components to the pcb
    [CanSat.kicad_pcb]
2025-12-10 Connected all components
    [CanSat.kicad_pcb]
2025-12-10 Rotated LoRa and updated readme
    [CanSat.kicad_pcb]
2025-12-15 Update of pcb
    [CanSat.kicad_pcb]
2026-01-22 Changed LoRa module to RFM98W 433MHz
    [CanSat.kicad_pcb, CanSat.kicad_sch, radio.kicad_sch]
2026-01-22 Fixed silkscreen overlap
    [CanSat.kicad_pcb]
2026-01-26 Added pin headers, debug headers, changed power source
    [CanSat.kicad_pcb, CanSat.kicad_sch]
2026-02-17 Added BOM to readme
    [CanSat.kicad_sch]
2026-03-07 Changed LoRa footprint + signed the PCB + added a on/off button
    [CanSat.kicad_pcb, CanSat.kicad_sch]
2026-03-11 Fixed design flaw with with components that MCU depends on
    [CanSat-CuBottom.gbr, CanSat-CuTop.gbr, CanSat-EdgeCuts.gbr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]
2026-03-13 Changed connectors
    [CanSat-CuBottom.gbr, CanSat-CuTop.gbr, CanSat-EdgeCuts.gbr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]
2026-03-13 Readme Update
    [CanSat-CuBottom.gbr, CanSat-CuTop.gbr, CanSat-EdgeCuts.gbr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]
2026-03-13 changed buzzer circuit and capacitor footprints
    [CanSat.kicad_pcb, CanSat.kicad_sch, rp2350a.kicad_sch]
2026-03-13 added Q1 part number
    [CanSat.kicad_pcb, CanSat.kicad_sch]
2026-03-13 updated spacing
    [CanSat-CuBottom.gbr, CanSat-CuTop.gbr, CanSat-EdgeCuts.gbr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]
2026-03-13 Changed QSPI and added pull-ups on i2c
    [CanSat-CuBottom.gbr, CanSat-CuTop.gbr, CanSat-EdgeCuts.gbr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]
2026-03-26 Fixed USB data lines
    [CanSat.kicad_pcb, CanSatrm.xlsx, rp2350a.kicad_sch]
